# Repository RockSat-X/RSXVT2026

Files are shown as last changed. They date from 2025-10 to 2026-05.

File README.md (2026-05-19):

# Virginia Tech RockSat-X 2026 Project.

> [!IMPORTANT]
> Quick link to:
> - [Wallops Testing Procedure](#wallops-testing-procedure).
> - [Remove-Before-Flight Procedure](#remove-before-flight-procedure).
>
> Also check out the [RSXVT2026 Wiki](https://github.com/RockSat-X/RSXVT2026/wiki)!

&nbsp;

# Mission Overview.

Our experiment aims to evaluate the use of optical navigation
with Commercial-off-the-Shelf (COTS) products for use in spaceflight applications.
To conduct the experiment,
an autonomous attitude determination and control system (ADCS)
employing an optical navigation system (ONS)
will be designed to control a 1U CubeSat,
codenamed **Commercial Optical Navigation Satellite (CONSat)**.

The 2024 NASA Civil Space Shortfall Ranking lists 9 out of the top 30 shortfalls
as limitations with autonomous deep space navigation.
With recent advancements in computing and ML capabilities,
optical navigation could revolutionize deep space navigation.
Our team aims to address some of the challenges facing the space industry
by designing a cost-effective ADCS that would rely primarily on conditions
only available in deep space.

The CONSat vehicle's Optical Navigation System (ONS) has:
- OpenMV H7+.
- VN-100 IMU / AHRS.

The operating principle of the CONSat will be to:
1. Capture image and isolate target.
2. Perform LoS measurements to estimate attitude.
3. Blend LoS solution with IMU / AHRS solution.
4. Reorient spacecraft to align to target.

The target will be the Earth's horizon as seen at ~190 km apogee.

&nbsp;

# High-Level System Overview.

<p align="center">
<kbd>

<br>
<br>
<em>Deck-plate integrated experiment.</em>
<br>
<br>
</kbd>
</p>&nbsp;

<p align="center">
<kbd>
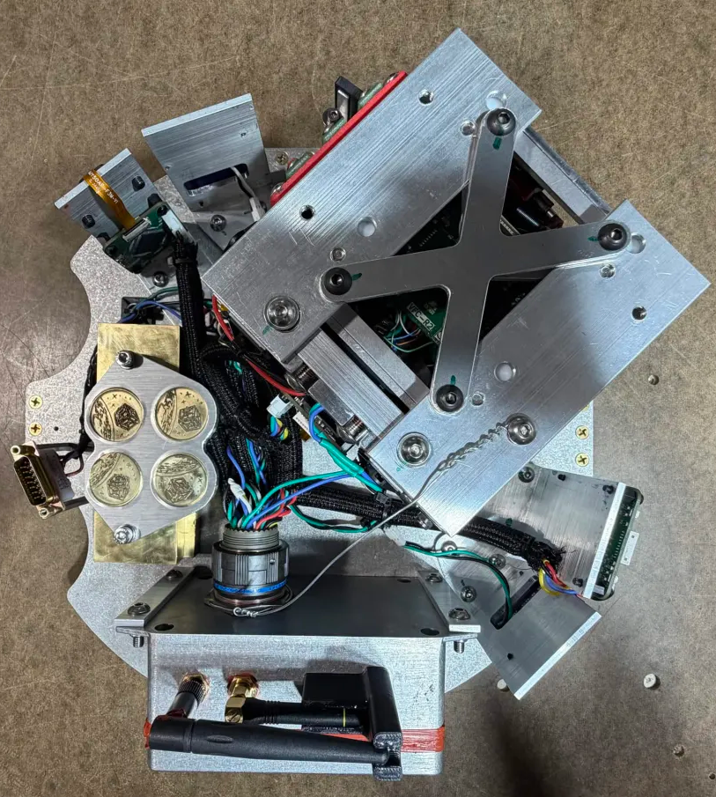
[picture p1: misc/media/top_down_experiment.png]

<br>
<br>
<em>Top-down view of the deck-plate integrated experiment.</em>
<br>
<br>
</kbd>
</p>&nbsp;

<p align="center">
<kbd>
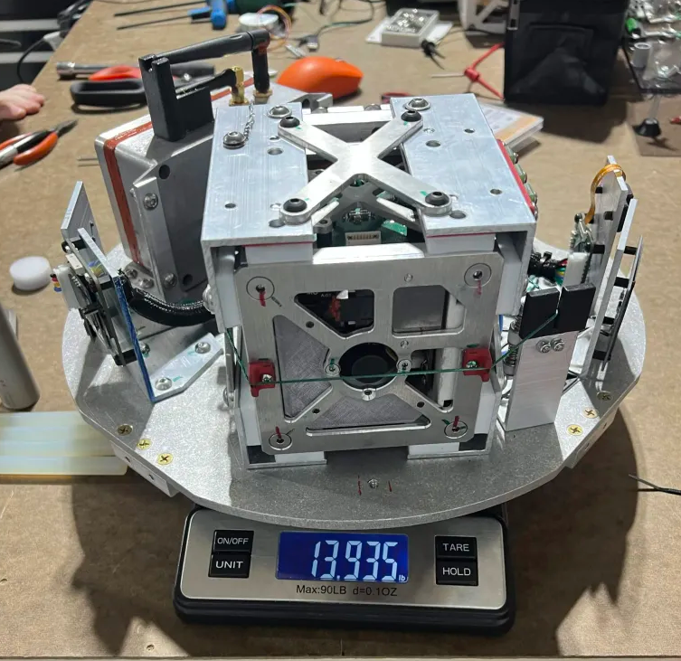
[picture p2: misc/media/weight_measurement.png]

<br>
<br>
<em>Weight of the deck-plate integrated experiment (13.935 pounds / 6.321 kilograms).</em>
<br>
<br>
</kbd>
</p>&nbsp;

<p align="center">
<kbd>
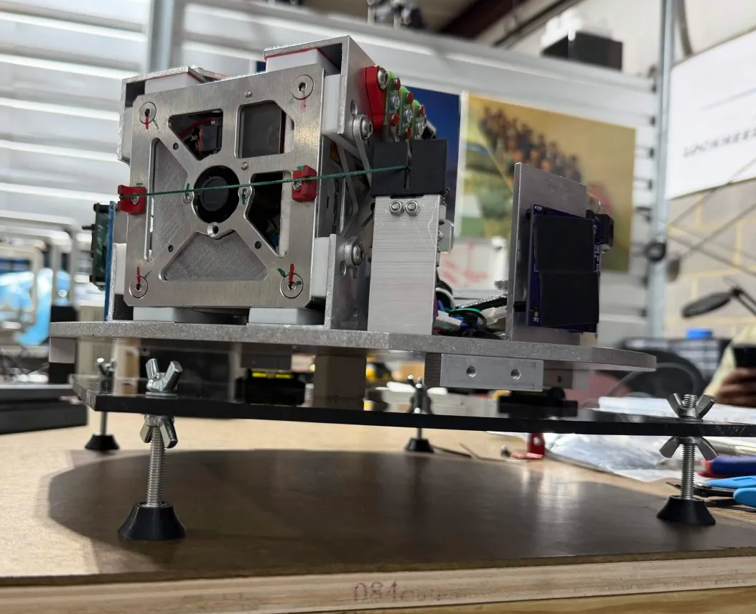
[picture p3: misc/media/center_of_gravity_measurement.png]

<br>
<br>
<em>Center of gravity of the deck-plate integrated experiment.</em>
<br>
<br>
</kbd>
</p>&nbsp;

<p align="center">
<kbd>
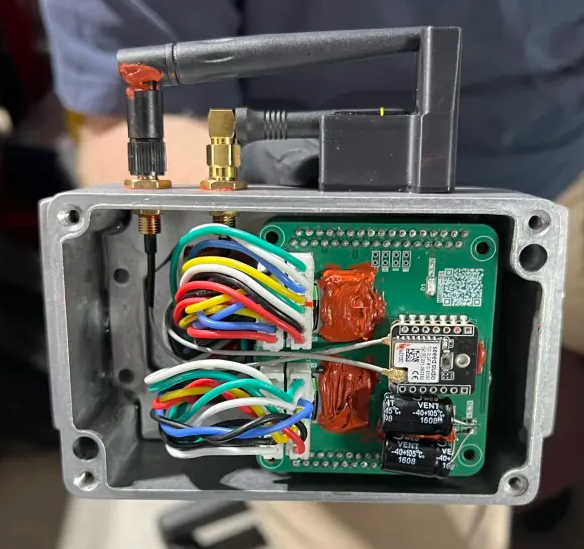
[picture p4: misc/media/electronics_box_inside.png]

<br>
<br>
<em>The inside of the main electronics box enclosure.</em>
<br>
<br>
</kbd>
</p>&nbsp;

<p align="center">
<kbd>
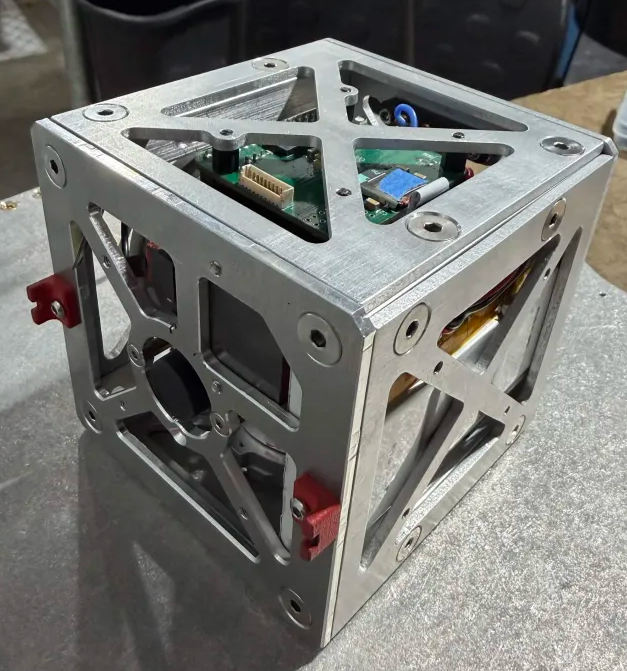
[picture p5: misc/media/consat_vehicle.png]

<br>
<br>
<em>CONSat vehicle.</em>
<br>
<br>
</kbd>
</p>&nbsp;

<p align="center">
<kbd>

<br>
<br>
<em>The inside of the CONSat vehicle.</em>
<br>
<br>
</kbd>
</p>&nbsp;

<p align="center">
<kbd>
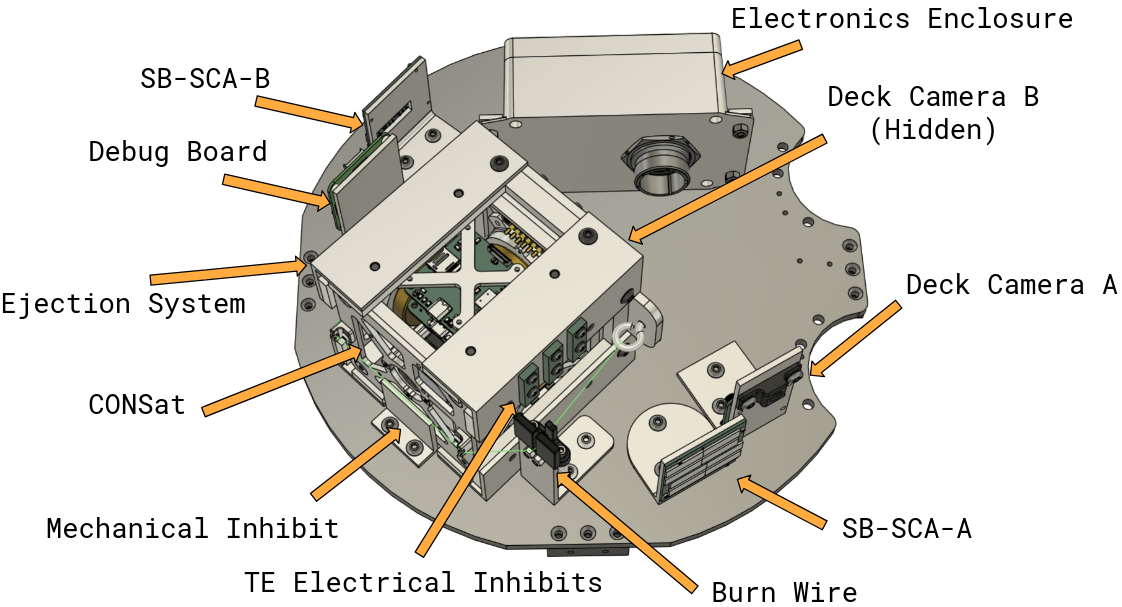
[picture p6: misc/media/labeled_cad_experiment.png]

<br>
<br>
<em>Labeled CAD model of the experiment.</em>
<br>
<br>
</kbd>
</p>&nbsp;

<p align="center">
<kbd>
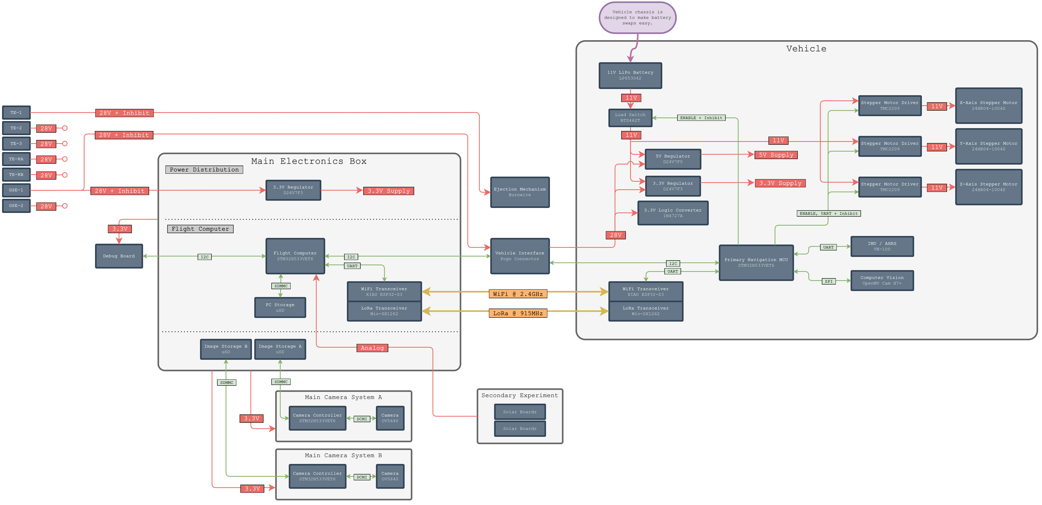
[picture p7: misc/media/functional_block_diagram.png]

<br>
<br>
<em>Functional block diagram of the CONSat experiment.</em>
<br>
<br>
</kbd>
</p>&nbsp;

## Main Camera System.

The experiment has two Main Camera Systems:
one placed before the ejection mechnism
and one next to a Solarboard by the burn-wire mechanism.

<p align="center">
<kbd>

<br>
<br>
<em>Main Camera System demonstration.</em>
<br>
<br>
</kbd>
</p>&nbsp;

The Main Camera System board has a single RGB LED.

| Color | Description |
| :---: | --- |
| White | Reformatting uSD card. |
| Magenta | Initializing uSD card. |
| Blue | Initializing OV5640 camera module. |
| Toggling green | Recording successfully. |
| Red | Main Camera System resetting. |

&nbsp;

The Main Camera System creates a binary blob file for each recording.
Use `cli.py parseVideo` to convert the binary blob file into an MP4 video.

&nbsp;

## Debug Board.

The Debug Board has a display to indicate the status of subsystems
from the perspective of the Main Flight Computer.
When the experiment is powered on via GSE-1,
the Debug Board will initialize and play the Nokia buzzer tune.
The display will also periodically invert color;
this is just to indicate that the Debug Board MCU is still running.

<p align="center">
<kbd>

<br>
<br>
<em>Debug board demonstration.</em>
<br>
<br>
</kbd>
</p>&nbsp;

The Debug Board displays the following information.

| Field | Description |
| :---: | --- |
| `DB-T` | Time elapsed since the debug board was powered on. |
| `MFC-T` | Time elapsed since the Main Flight Compiuter was powered on. |
| `SCB-A` | Voltage of SB-SCA. |
| `SCB-B` | Voltage of HP-SCA. |
| `te1` | Whether or not Main Flight Computer is detecting TE-1. |
| `vehicle` | Whether or not Main Flight Computer is communicating with the Vehicle Flight Computer through the vehicle interface. |
| `esp32` | Whether or not Main Flight Computer is receiving ESP-NOW data packets. |
| `lora` | Whether or not Main Flight Computer is receiving LoRa data packets. |
| `logger`  | Whether or not Main Flight Computer is saving data to its uSD card. |

If the Debug Board has not received the first debug packet from the Main Flight Computer yet,
then the field values will either be `???` or `nan` to indicate this.

> [!IMPORTANT]
> A known issue with the Debug Board's display is that it is not resettable.
> That is, if the Debug Board MCU has a communication issue with the display driver,
> there's a small possibility that the display ends up in a corrupted state.
> This may appear as the screen being darker, the resolution looking off,
> or is completely blank.
> The MCU has no way to fix this,
> but power-cycling will resolve this rare issue if it ever happens.

&nbsp;

The debug board has four RGB LEDs.

| Label | Position | Description |
| :---: | :---: | --- |
| `A` | Top Right | Flashes colors when the buzzer is being driven; this is just an extra indicator that's useful for when the buzzer is mute. |
| `B` | Top Left | White when the Main Flight Computer hasn't sent the first debug packet to the Debug Board yet; red when there's a bad status to be aware of such as the Main Flight Computer not having received RF data in a while. |
| `C` | Bottom Right | Toggles red when the Main Flight Computer hasn't sent a debug packet in a while; toggles green when a debug packet has been received. |
| `D` | Bottom Left  | White when the uSD card is being formatted; magenta when the Debug Board is failing to initialize the uSD card; toggles green periodically when data is successfully being logged to the uSD card. |

> [!IMPORTANT]
> If the Debug Board encounters an irrecoverable error,
> it'll panic and indicate this by flashing all LEDs red.
> The Debug Board should eventually reset itself and continue on as normal.

&nbsp;

The debug board plays the following buzzer tunes.

| Tune | Description |
| :---: | --- |
| [Nokia ](./misc/media/nokia.wav ) | Debug Board is initializing (e.g. just powered on from GSE-1). |
| [Hazard ](./misc/media/hazard.wav ) | Debug Board hasn't received a debug packet from the Main Flight Computer in a while. |
| [Up and Down](./misc/media/up_and_down.wav) | `te1` is active (i.e. burn-wire is going). |
| [Deep Beep  ](./misc/media/deep_beep.wav  ) | Main Flight Computer is reporting a bad status (e.g. haven't received RF data in a while) |
| [Tetris ](./misc/media/tetris.wave ) | The Debug Board's uSD card is being reformatted. |

To mute the buzzer, leave the header above the buzzer open.
To enable the buzzer, have a jumper shorting two adjacent pins;
which pins are shorted determines the volume of the buzzer.

&nbsp;

The uSD card is optional to the operation of the Debug Board.
The Debug Board uses LED D to indicate that it's successfully saving log data.

<p align="center">
<kbd>

<br>
<br>
<em>
To load a uSD card, lift the connector lid up,
<br>
place the uSD card,
and slide the lid down to secure it.
</em>
<br>
<br>
</kbd>
</p>&nbsp;

<p align="center">
<kbd>
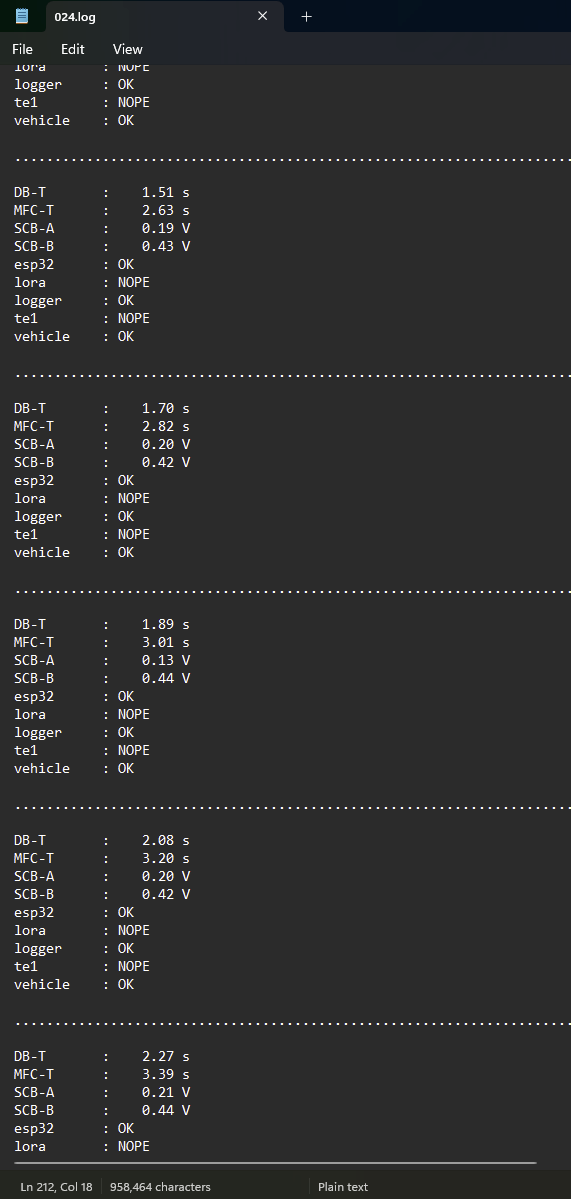
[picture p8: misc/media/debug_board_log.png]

<br>
<br>
<em>
The Debug Board creates an ASCII text file with <br>
the same information displayed on its screen.
</em>
<br>
<br>
</kbd>
</p>&nbsp;

## Vehicle Flight Computer.

The following table details the corresponding buzzer tune and RGB LED behavior for when a Vehicle Flight Computer diagnostic is reported.

| Severity | Tune | RGB LED | Description |
|:-:| :---: | :---: | --- |
| :bangbang: | [Ambulance  ](./misc/media/ambulance.wav ) | Fast toggling red | TMC2209 stepper motor drivers are failing initialization. This could be due to bad ribbon cable connection, dead batteries, inhibited batteries, or something else. |
| :warning: | [Heartbeat  ](./misc/media/heartbeat.wav ) | Slow toggling red | Vehicle Flight Computer has saturated a motor's RPM velocity. |
| :warning: | [Tetris ](./misc/media/tetris.wav ) | Slow toggling white | Vehicle Flight Computer is reformatting the uSD card. |
| :warning: | [Mario ](./misc/media/mario.wav ) | Fast toggling white | Resetting the Vehicle ESP32 due to an issue with it. |
| :warning: | [Three Tone ](./misc/media/three_tone.wav ) | Fast toggling white | Resetting the Vehicle OpenMV due to an issue with it. |
| :bangbang: | [Hazard ](./misc/media/hazard.wav ) | Fast toggling blue  | Communication issue with VN-100. |
| :white_check_mark: | [Nokia ](./misc/media/nokia.wav ) | Slow toggling white | Vehicle Flight Computer detecting that the vehicle has been redocked. |
| :white_check_mark: | [Birthday ](./misc/media/birthday.wav ) | Slow toggling white | Vehicle Flight Computer detecting that the vehicle has been ejected. |
| :warning: | [Heavy Beep ](./misc/media/heavy_beep.wav ) | Toggling magenta | Initialization issue with uSD card. This is okay if no uSD card is loaded. |
| :white_check_mark: | [Burp ](./misc/media/burp.wav ) | Blue blink | VN-100 communication okay. |
| :white_check_mark: | [Chirp ](./misc/media/chirp.wav ) | Green blink | uSD card logging okay. |
| :white_check_mark: | [Waking Up  ](./misc/media/waking_up.wav ) | None | Vehicle Flight Computer initializing (i.e. on activation of GSE-1); vehicle batteries are enabled at end of buzzer tune. |
| :white_check_mark: | [Star Wars  ](./misc/media/starwars.wav ) | None | Vehicle Flight Computer performing a dock shutdown (i.e. about to turn vehicle batteries off and resetting). |

| Severity | Description |
| :---: | --- |
| :bangbang:  | Something is likely very problematic and should be addressed as soon as possible. |
| :warning:  | A non-fatal or recoverable issue. |
| :white_check_mark:  | Positive or expected indicator of a working system. |

The three pin header on the Vehicle Flight Computer can be left open to mute the buzzer,
otherwise short a pair of adjacent pins to determine the volume of the buzzer.

&nbsp;

The Vehicle Flight Computer board also has an optional uSD card slot for log data.

<p align="center">
<kbd>
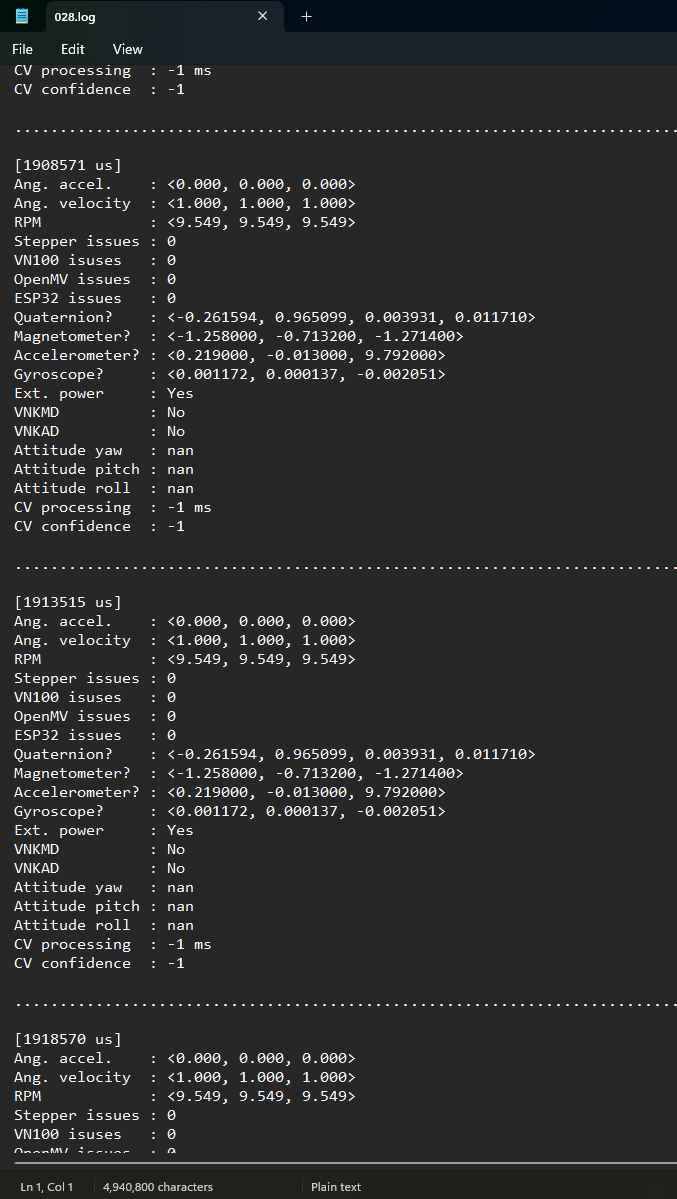
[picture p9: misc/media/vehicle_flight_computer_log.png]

<br>
<br>
<em>
The Vehicle Flight Computer creates an ASCII text file with information <br>
like VN-100 IMU data, CVT results, current motor velocities, and so on.
</em>
<br>
<br>
</kbd>
</p>&nbsp;

&nbsp;

## OpenMV H7+.

The OpenMV H7+ has a single RGB LED.

| RGB LED | Description |
| :---: | --- |
| Flashing blue | The CVT algorithm hasn't detected the horizon yet. |
| Flashing green | The CVT algorithm has found the horizon. |

Each toggle of the RGB LED represents an entire image being captured, processed, and transmitted to the Vehicle Flight Computer.
Because JPEG image compression is used,
if the OpenMV H7+'s camera lens is covered (e.g. by a finger),
the blinking of the RGB LED will be much faster.

If the OpenMV H7+'s RGB LED is not blinking, then it's very likely the program is not running,
but the Vehicle Flight Computer should reset the OpenMV H7+ eventually after a time-out period.

No other colors or behavior should be expected from the RGB LED or the OpenMV H7+ module as a whole.

&nbsp;

## Vehicle Power Distribution System.

The Vehicle Power Distribution System has LED indicators to be aware of.

| LED | Description |
| :---: | --- |
| Bright white | Vehicle interface providing power to the vehicle, thus this LED should be active if and only if the vehicle is docked and GSE-1 is active. |
| Yellow | Vehicle Flight Computer has enabled on-board battery power. The LED should be off when the Vehicle Flight Computer is initializing but should eventually turn on, unless the vehicle battery inhibit is in place, to which this LED will never turn on. |

The Vehicle Power Distribution System has three jumpers to be aware of.

<p align="center">
<kbd>
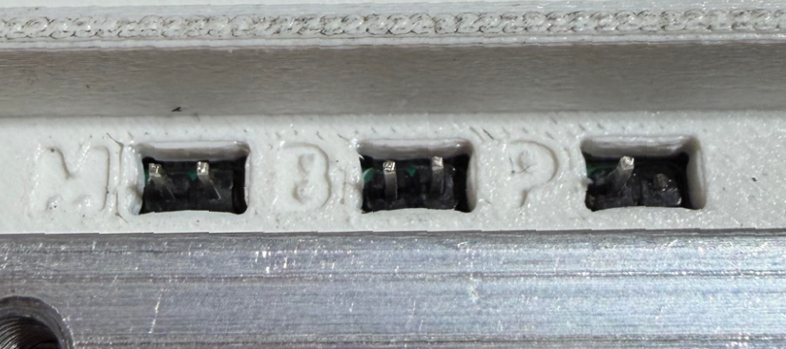
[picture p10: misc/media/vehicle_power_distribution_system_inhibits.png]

<br>
<br>
<em>
First jumper on the left denoted with "M" as in "Motor Inhibit". <br>
Second jumper in the middle denoted with "B" as in "Battery Inhibit". <br>
Third jumper on the right denoted with "P" as in "Power". <br>
Note that the third "Power" jumper should only have its <br>
first left pin and the second right pin is broken off.
</em>
<br>
<br>
</kbd>
</p>&nbsp;

| Jumper | Activation | Description |
| :---: | - | - |
| "M" | Use a shorting 2-pin jumper with pull tab. | Disable the control of the stepper motors. Vehicle Flight Computer can still initialize and operate, but reaction wheels will not spin. This is used to conserve battery charge, if needed. |
| "B" | Use a shorting 2-pin jumper with pull tab. | Disable the usage of the vehicle batteries. Vehicle Flight Computer can still initialize and operate via external power through the vehicle interface (i.e. GSE-1), but will immediately unpower upon being undocked. This can also be used to turn off the vehicle manually. |
| "P" | Use jumper wire to connect the pin to one of the vehicle batteries' positive terminal and wait several seconds. | Forces the usage of vehicle battery power, thus the Vehicle Flight Computer will initialize. This is to turn the vehicle on without relying on external power. |

> [!TIP]
> A quick way to turn off the vehicle is by using an Allen key to short the middle "B" jumper.

&nbsp;

# RF Verification.

During sequence testing and particularly GPS Roll-Out,
it's critical to verify that RF systems are working as intended
and to communicate this to NASA.

The easiest way to do this is to use the [Debug Board](#debug-board).
The screen will indicate if the Main Flight Computer is receiving RF data from the ESP32 and/or LoRa.
If the Debug Board is loaded with a uSD card,
the RF status will also be logged over time.

A more robust way to verify RF is to use the TinySA Spectrum Analyzer.
There are two particular frequency bands of interest.
| Link  | Center | Bandwidth | Start | End |
| :---: | :---: | :---: | :---: | :---: |
| ESP32 | 2.472 GHz | 20 MHz | 2.462 GHz | 2.482 GHz |
| LoRa  | 920 MHz | 125 kHz | 919.9375 MHz | 920.0625 MHz |

Configure the spectrum analyzer to observe these frequencies.

<p align="center">
</kbd>
<kbd>

<br>
<br>
<em>
Spectrum analyzer demonstration.
</em>
<br>
<br>
</kbd>
</p>&nbsp;

You should see a reading similar the following figures:

<p align="center">
<kbd>
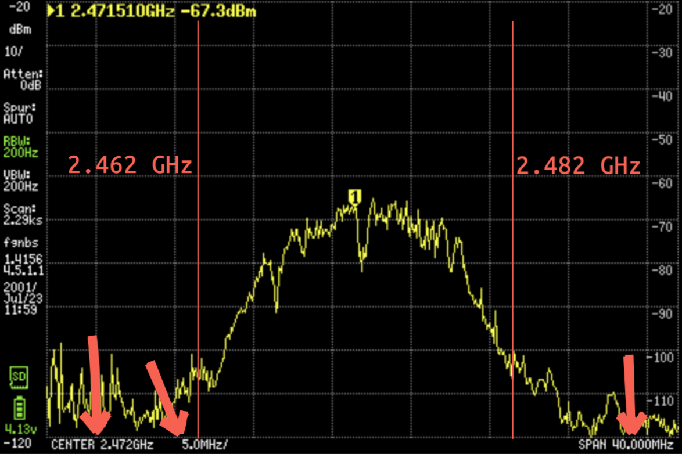
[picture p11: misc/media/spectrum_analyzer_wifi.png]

<br>
<br>
<em>
Spectrum analyzer measurement for the ESP32 link.
</em>
<br>
<br>
</p>
<p align="center">
</kbd>
<kbd>
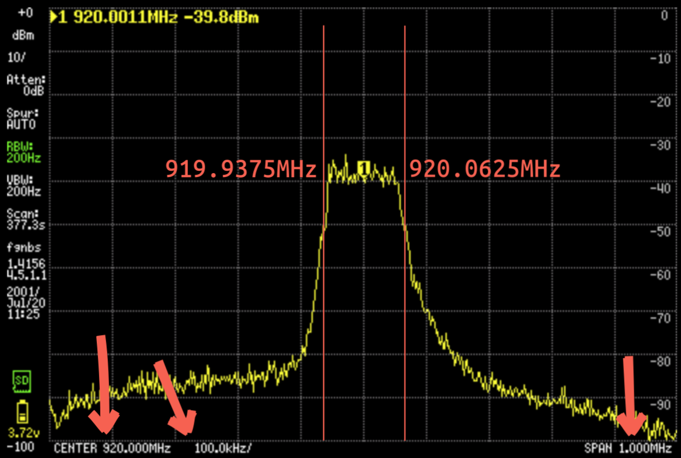
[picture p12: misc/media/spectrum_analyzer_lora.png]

<br>
<br>
<em>
Spectrum analyzer measurement for the LoRa link.
</em>
<br>
<br>
</kbd>
</p>&nbsp;

> [!IMPORTANT]
> The measurements shown in the figures were taken with an RBW value of 200 Hz;
> this makes the measurement more accurate but at the cost of being extremely slow.
> It's probably more productive to use an auto RBW value so measurements can be done quickly.
> Just as long there is an expected peak within frequency bands, all is good.

The RF verification process and expectations should be roughly as follows:

1. Before the experiment is powered on via GSE-1, no RF transmission is detected within the frequency bands.

2. Shortly after the experiment is powered on via GSE-1,
ESP32 and LoRa transmission can be seen within the frequency bands.

3. RF transmission is sustained for at least the duration of a full mission;
if applicable, the RF transmission should still be sustained even if the vehicle has ejected or becomes undocked.

4. RF transmission is sustained even when main has powered off (i.e. GSE-1 deactived)
as the vehicle will continue transmitting via battery power.

5. RF transmission is no longer detected once the vehicle has powered off
(either by using the vehicle battery inhibit or through a docked reset).

&nbsp;

# Wallops Testing Procedure.

The following table summarizes the primary configurations needed to be set for tests done at Wallops.

| Expected Date | Test | Allow Ejection? | Enable TE-1? | Enable Main GSE-1? | Enable Vehicle GSE-1? |
| :---: | :---: | :-: | :-: | :-: | :-: |
| May 17th, 2026; Sunday | Pre-Flight Seq. | :white_check_mark: | :white_check_mark: | :white_check_mark: | :white_check_mark: |
| May 18th-19th, 2026; Monday-Tuesday | Pre-Vibe All-Fire Seq. | :white_check_mark: | :white_check_mark: | :white_check_mark: | :white_check_mark: |
| May 18th-19th, 2026; Monday-Tuesday | Pre-Vibe No-Fire Seq. | :x: | :x: | :white_check_mark: | :white_check_mark: |
| May 19th, 2026; Tuesday | Pre-Vibe Back Up Seq. | :x: | :x: | :white_check_mark: | :white_check_mark: |
| May 20th-21st, 2026; Wednesday-Thursday | Vibration Testing | :white_check_mark: | :white_check_mark: | :white_check_mark: | :white_check_mark: |
| May 22nd, 2026; Friday | Post-Vibe All-Fire Seq. | :white_check_mark: | :white_check_mark: | :white_check_mark: | :white_check_mark: |
| May 22nd, 2026; Friday | Post-Vibe No-Fire Seq. | :x: | :x: | :white_check_mark: | :white_check_mark: |
| May 22nd, 2026; Friday | Post-Vibe Back Up Seq. | :x: | :x: | :white_check_mark: | :white_check_mark: |
| May 22nd, 2026; Friday | GPS Roll-Out | :x: | :x: | :white_check_mark: | :white_check_mark: |
| June 19th, 2026; Friday | Final All-Fire Seq. | :white_check_mark: | :white_check_mark: | :white_check_mark: | :white_check_mark: |
| June 19th, 2026; Friday | Final No-Fire Seq. | :x: | :x: | :white_check_mark: | :white_check_mark: |
| June 19th, 2026; Friday | Final Back Up Seq. | :x: | :x: | :white_check_mark: | :white_check_mark: |

To allow ejection ( :white_check_mark: ),
ensure the mechanical inhibit in front of the ejection mechanism is removed.

To prevent ejection ( :x: ),
ensure the mechanical inhibit is secured in front of the ejection mechanism.

To have TE-1, Main GSE-1, or Vehicle GSE-1 be enabled ( :white_check_mark: ),
insert a screw into the corresponding electrical screw switch on the side of the ejection mechanism.
Verify short-circuit with a multimeter.

To have TE-1, Main GSE-1, or Vehicle GSE-1 be disabled ( :x: ),
ensure a screw is not inserted into the corresponding electrical screw switch.
Verify open-circuit with a multimeter.

> [!IMPORTANT]
> The experiment must be put into flight-ready configuration during vibration testing.
> This means all electrical screw switches should be enabled and no mechanical inhibit present.
> Any loose components such as external uSD cards and jumpers should be removed (see [RBF procedures](#remove-before-flight-procedure)).
> Screws should be applied with blue Loctite.
>
> It should also be noted that Wallops will only provide GSE-1 and there will be no TE-1 power
> during this vibration test (this also applies to GPS Roll-Out).

> [!IMPORTANT]
> The purpose of the electrical screw switches for Main GSE-1 and Vehicle GSE-1 is for flexibility.
> In the event that we need to ensure that the main avionics and/or vehicle does not power on,
> we have these as a way to do so.

&nbsp;

# Remove-Before-Flight Procedure.

The following steps are to be carried out in order with minimal deviations after all final sequence tests are done.

> [!IMPORTANT]
> Pre-RBF procedure checklist:
> - Multimeter.
> - Three fully charged EEMB LP653042 3.7V 820mAh batteries.
> - Allen key kit.
> - Red Loctite.
> - Tweezers.
> - Needle-nose pliers.
> - Phillips screwdriver.

&nbsp;

## 1. Take out vehicle.

Remove the ejection inhibit if still in place.
The ejection inhibit will not be used again,
so store it away in a secure location.

Take out the burn-wire mechanism in order to release the vehicle from the ejection mechanism.
Place the burn-wire mechanism in a secure location.

Carefully undock vehicle and place it down on a table to be worked on.

&nbsp;

## 2. Replace vehicle batteries.

Go to the side of the vehicle where the batteries are stored.

<p align="center">
<kbd>
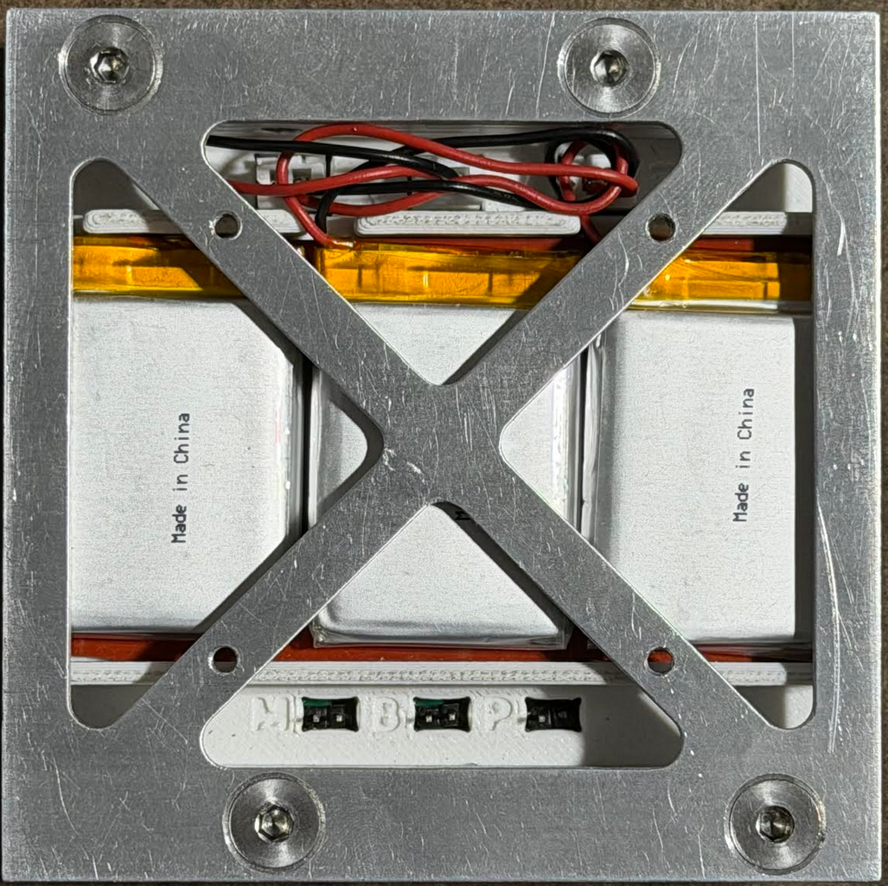
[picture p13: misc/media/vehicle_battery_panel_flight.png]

<br>
<br>
<em>
Side of the vehicle where the batteries are stored.
</em>
<br>
<br>
</kbd>
</p>&nbsp;

Take off the panel.
Place the panel and screws in a secure location.

<p align="center">
<kbd>
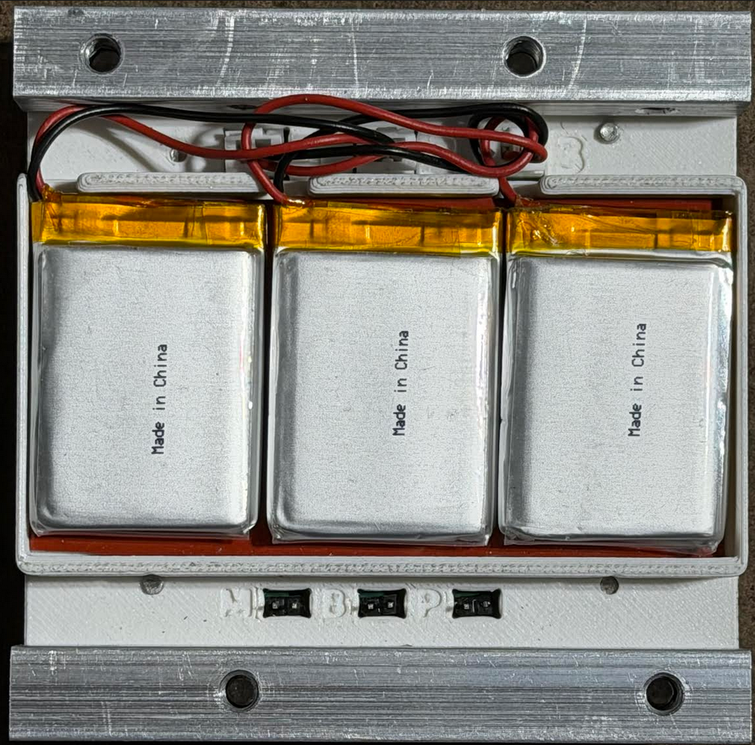
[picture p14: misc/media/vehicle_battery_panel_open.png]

<br>
<br>
<em>
Panel that secured the vehicle's batteries removed.
</em>
<br>
<br>
</kbd>
</p>&nbsp;

Take out the old vehicle batteries.
It is okay to tug on the cable to do so if excessive force is not used.
Make sure to place the old vehicle batteries somewhere secure so it will not be confused with the new batteries.

<p align="center">
<kbd>
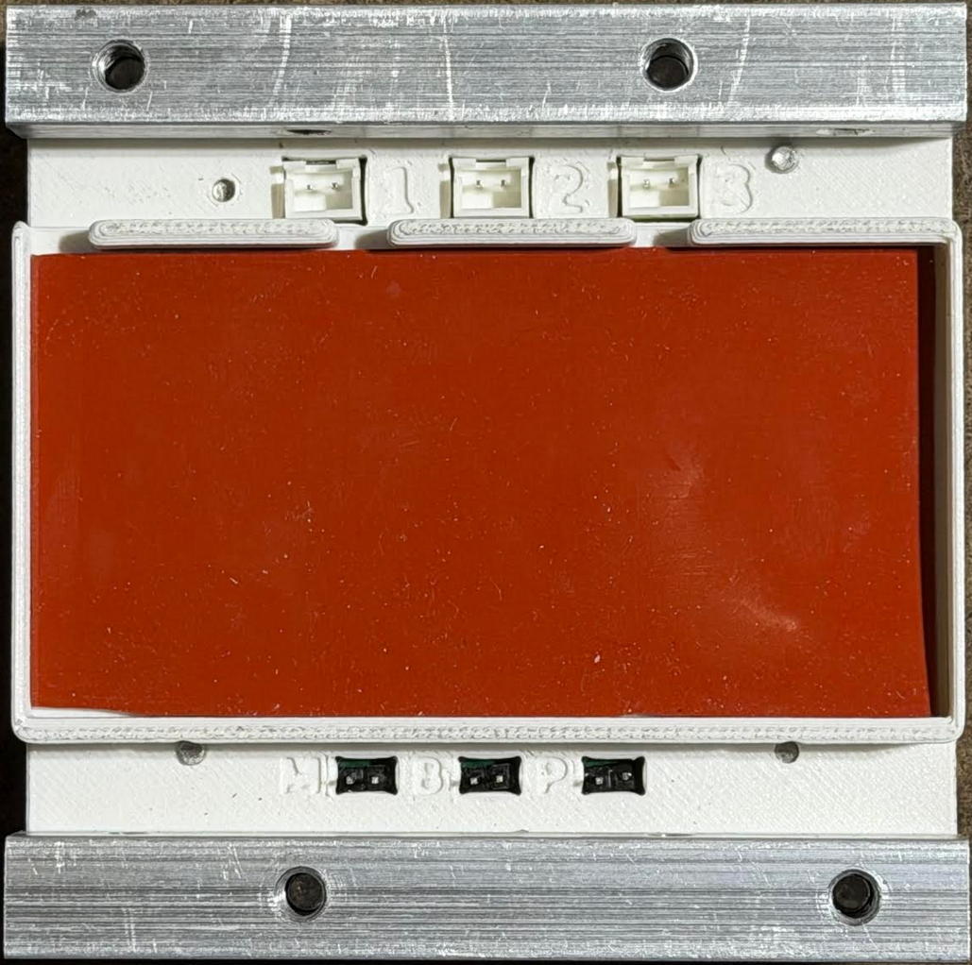
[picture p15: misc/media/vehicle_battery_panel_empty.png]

<br>
<br>
<em>
Vehicle batteries removed.
</em>
<br>
<br>
</kbd>
</p>&nbsp;

Verify that the new batteries (EEMB LP653042 3.7V 820mAh) are fully charged.

<p align="center">
<kbd>
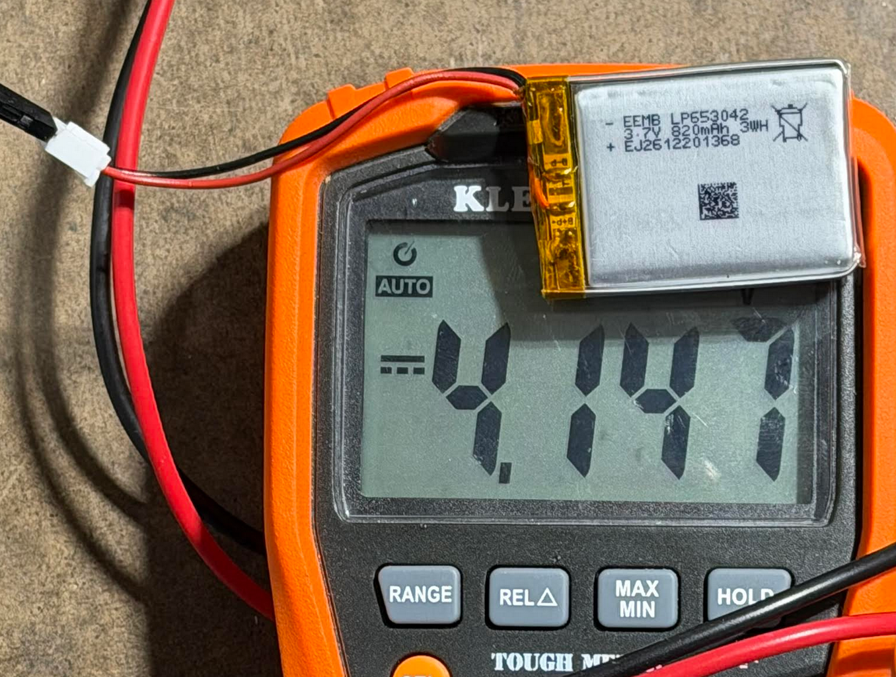
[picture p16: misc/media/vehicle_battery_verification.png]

<br>
<br>
<em>
A fully charged vehicle battery should have at least 4V.
</em>
<br>
<br>
</kbd>
</p>&nbsp;

Verify that the new batteries have a JST-XH plug of the correct polarity.

<p align="center">
<kbd>
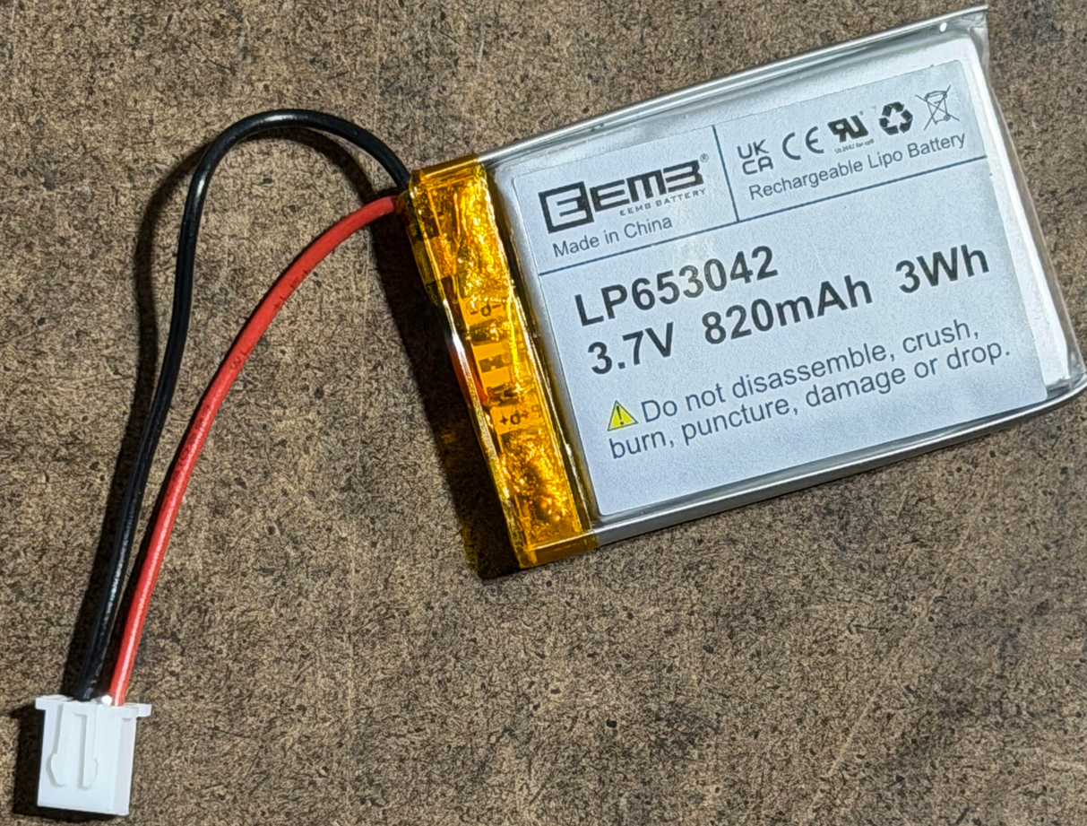
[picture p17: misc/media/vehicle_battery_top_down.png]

<br>
<br>
<em>
Note the plug polarity.
</em>
<br>
<br>
</kbd>
</p>&nbsp;

Put in the new vehicle batteries.
The order in which the vehicle batteries are connected does not matter.
Ensure the cables are well tucked to prevent them being crushed by the panel.

<p align="center">
<kbd>

<br>
<br>
<em>
Vehicle batteries replaced.
</em>
<br>
<br>
</kbd>
</p>&nbsp;

Place and align the vehicle panel with the pillar's screw holes and verify
that the battery cables will not be crushed.

<p align="center">
<kbd>
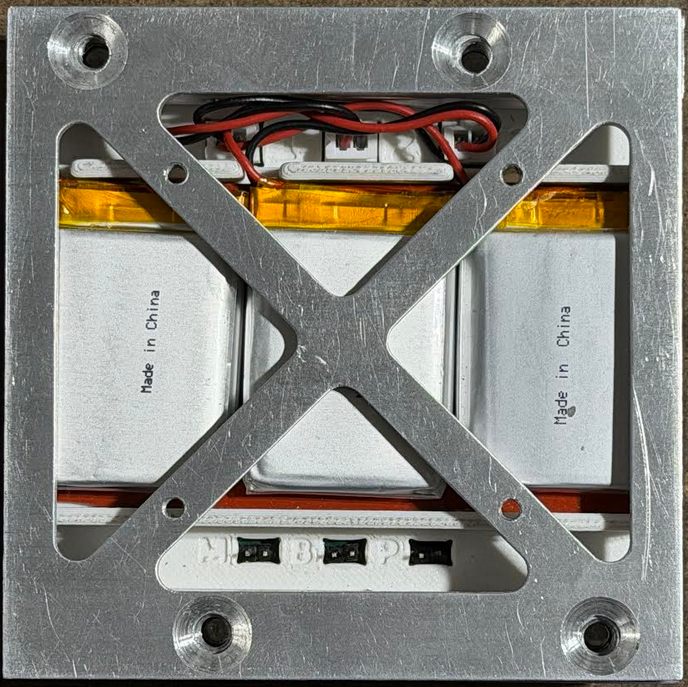
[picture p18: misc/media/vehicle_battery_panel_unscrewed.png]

<br>
<br>
<em>
Vehicle panel aligned on top but not yet screwed.
</em>
<br>
<br>
</kbd>
</p>
<p align="center">
<kbd>
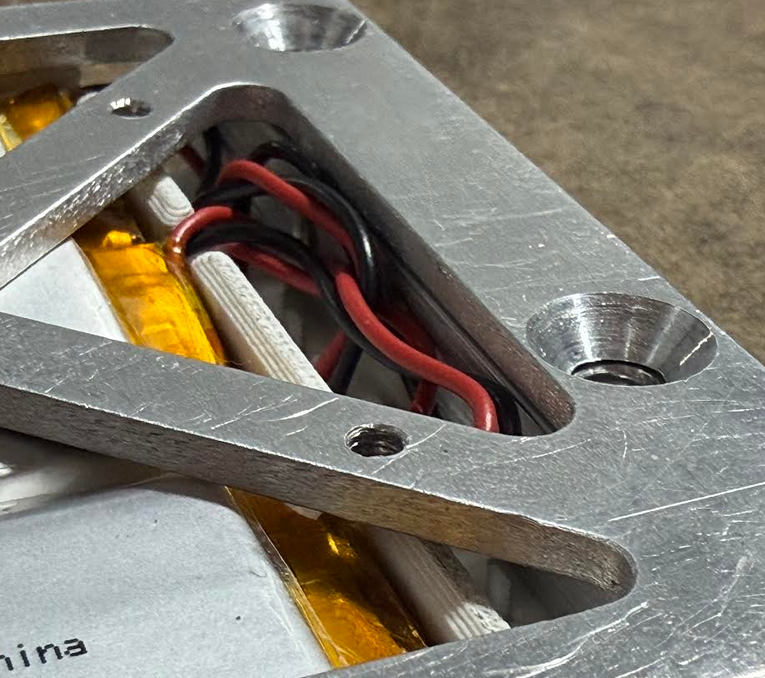
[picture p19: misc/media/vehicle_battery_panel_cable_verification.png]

<br>
<br>
<em>
Battery cables tucked securely and not between the panel and pillar.
</em>
<br>
<br>
</kbd>
</p>&nbsp;

Apply red Loctite to the threads and reinsert screws to secure the panel.

<p align="center">
<kbd>

<br>
<br>
<em>
Side of the vehicle where the batteries are stored.
</em>
<br>
<br>
</kbd>
</p>&nbsp;

## 3. Remove vehicle jumper inhibits.

Ensure the vehicle's jumpers for disabling motors, disabling batteries, and forcing vehicle power-on
are all open-circuit as depicted below.

<p align="center">
<kbd>

<br>
<br>
<em>
Vehicle jumpers in flight configuration.
</em>
<br>
<br>
</kbd>
</p>&nbsp;

## 4. Redock vehicle.

Reinsert vehicle into the ejection mechanism.
Make certain that the vehicle is in the correct orientation.
Verify that the vehicle interface connectors are aligned.

Put the previously removed burn-wire mechanism
back onto the deck-plate to secure the vehicle in the ejection mechanism.
Apply red Loctite to screws during this process.

Visually verify and test that the vehicle is well secured
by the ejection mechanism and burn-wire rope.

&nbsp;

## 5. Remove external uSD connector lids and jumpers.

To prevent vibration risks,
the Vehicle Flight Computer and Debug Board should have the lid of their uSD connectors be taken off.
The pin header for the buzzer should also be left as an open circuit.

<p align="center">
<kbd>
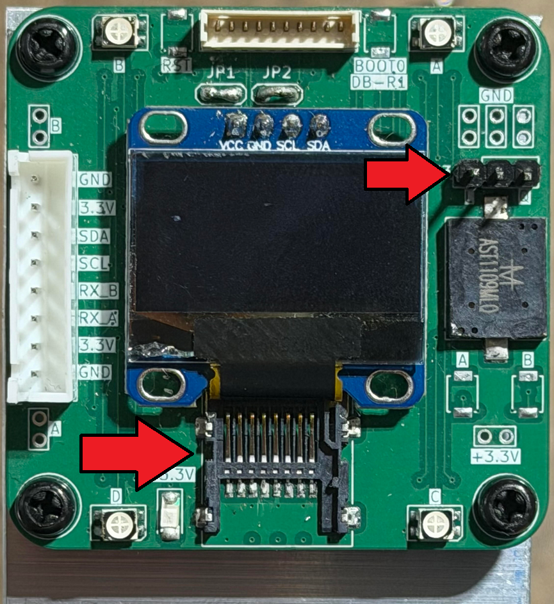
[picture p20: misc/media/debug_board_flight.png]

<br>
<br>
<em>
Debug Board without uSD card connector lid and buzzer jumper.
</em>
<br>
<br>
</kbd>
</p>&nbsp;

<p align="center">
<kbd>
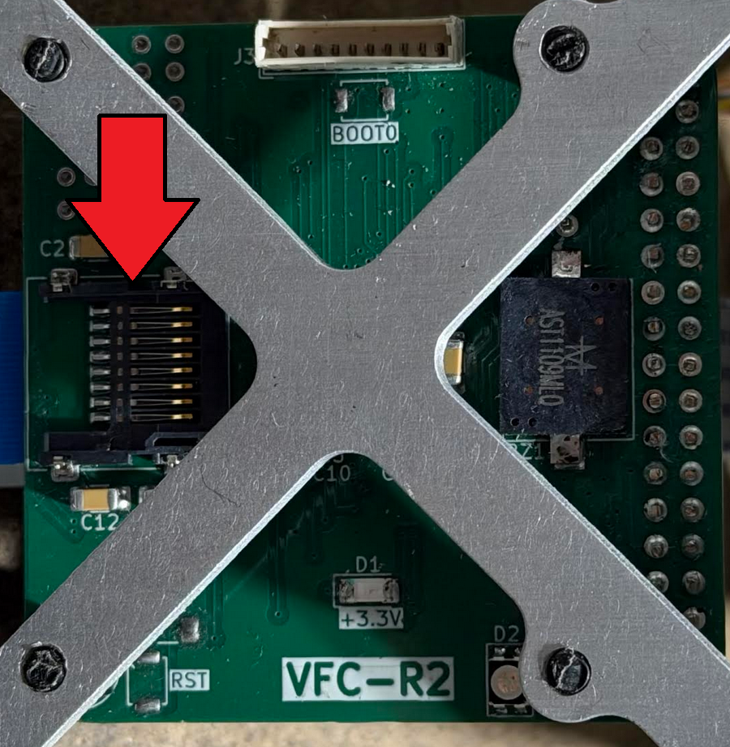
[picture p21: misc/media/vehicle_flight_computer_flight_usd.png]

<br>
<br>
<em>
Vehicle Flight Computer without uSD card connector lid.
</em>
<br>
<br>
</kbd>
</p>&nbsp;

<p align="center">
<kbd>
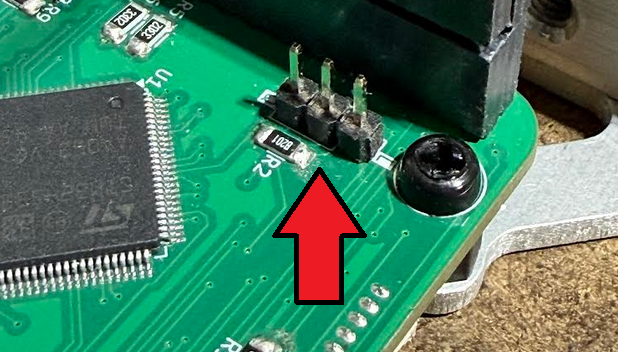
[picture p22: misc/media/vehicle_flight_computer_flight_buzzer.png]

<br>
<br>
<em>
Vehicle Flight Computer without buzzer jumper. <br>
Tweezers might be needed.
</em>
<br>
<br>
</kbd>
</p>&nbsp;

## 6. Enable electrical screw switches.

Insert screws with red Loctite into the three electrical screw switches
on the side of the ejection mechanism.

Verify connectivity of each electrical screw switch
by testing continuity of the two pads.

&nbsp;

## 7. Final checks.

> [!IMPORTANT]
> Verify that the following has been done:
> - New vehicle batteries has been put in.
> - Red Loctite has been applied to the vehicle's panel on the battery side.
> - Red Loctite has been applied to the burn-wire mechanism.
> - Red Loctite has been applied to the electrical screw switches.
> - Vehicle is well secured by the burn-wire rope and ejection mechanism as a whole.
> - No loose components like uSD card connector lids or jumpers are in place.
> - Electrical screw switches have the expected connectivity.

&nbsp;

# Burn-Wire Line Assembly.

These instructions describe how to fabricate the burnwire restraint lines
using 1 mm braided line and two overhand loop knots.

The finished burnwire line should have:
- Two looped ends.
- Approximately 12.75 in finished length.
- ±0.5 inch allowable tolerance.

Required materials:
- Tape measure.
- Dorisea Extreme Braid, 300 lb, 1 mm.
- Good scissors or sharp knife.

Use an _**Overhand Loop Knot**_ for both ends ([video tutorial](https://www.youtube.com/watch?v=7LSOyXJeUog)).

<p align="center">
<kbd>
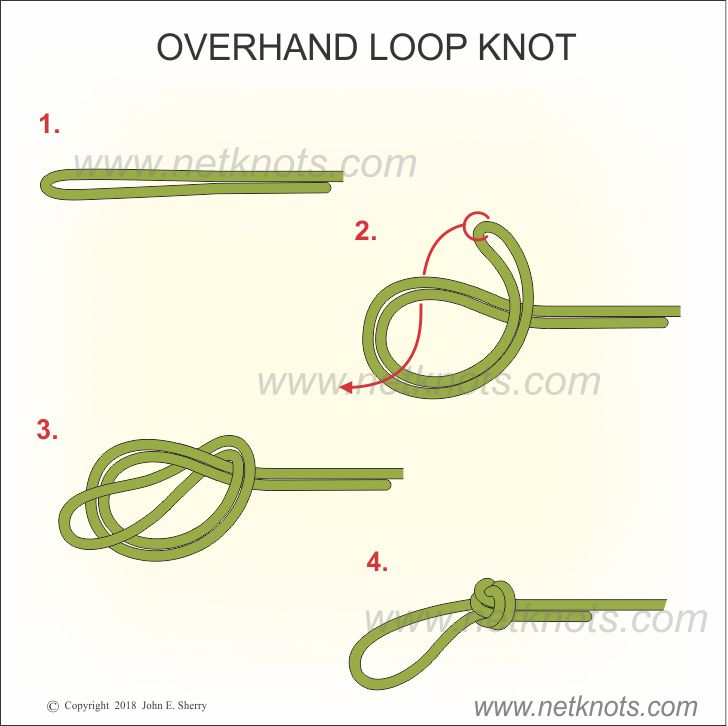
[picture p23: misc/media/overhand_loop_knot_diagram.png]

<br>
<br>
<em>
Overhand loop knot reference diagram.
</em>
<br>
<br>
</kbd>
</p>&nbsp;

## 1. Tie first loop.

Tie an overhand loop knot at the end of the line.
Target loop length of approximately 1 inch.
Leave a short tail after tightening the knot.

<p align="center">
<kbd>
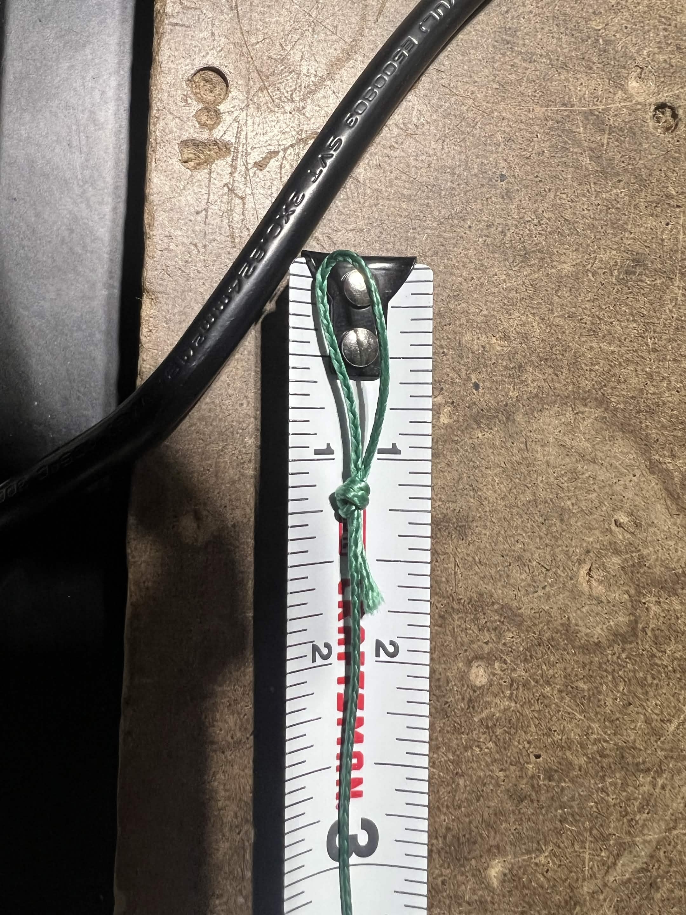
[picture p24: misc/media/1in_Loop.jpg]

<br>
<br>
<em>
1 inch loop.
</em>
<br>
<br>
</kbd>
</p>&nbsp;

## 2. Measure length.

Using the tape measure, measure _**13.5 inches from the tip of the loop**_.
Mark this location with a marker.

> [!IMPORTANT]
> _**Do NOT cut the line yet.**_

<p align="center">
<kbd>
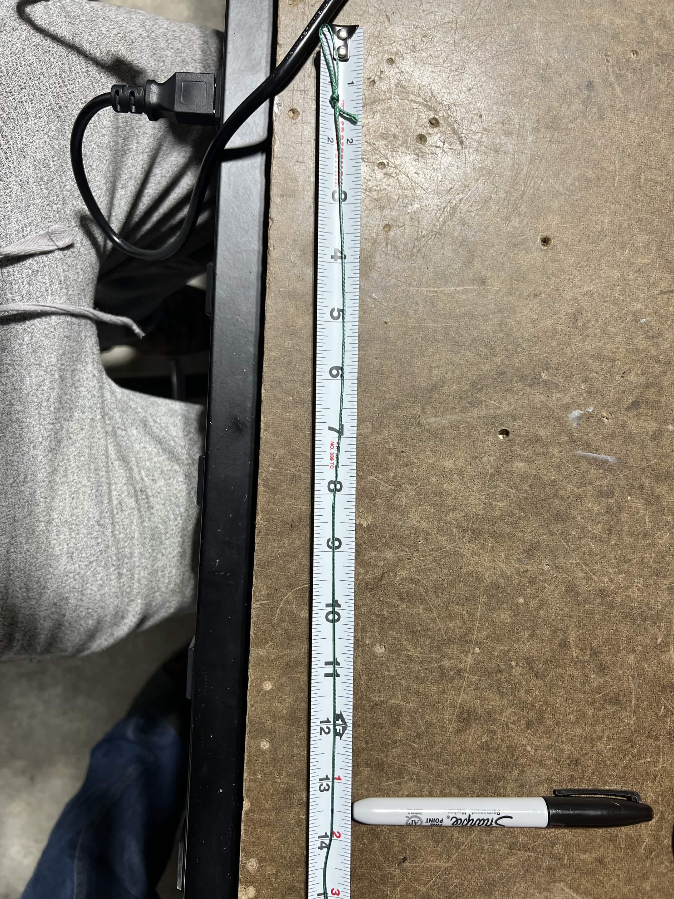
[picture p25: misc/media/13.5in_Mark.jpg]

<br>
<br>
<em>
13.5 inch mark.
</em>
<br>
<br>
</kbd>
</p>&nbsp;

## 3. Fold the line.

Fold the line in half at the 13.5 inch mark.
Ensure the marked location becomes the tip of the second loop.

<p align="center">
<kbd>
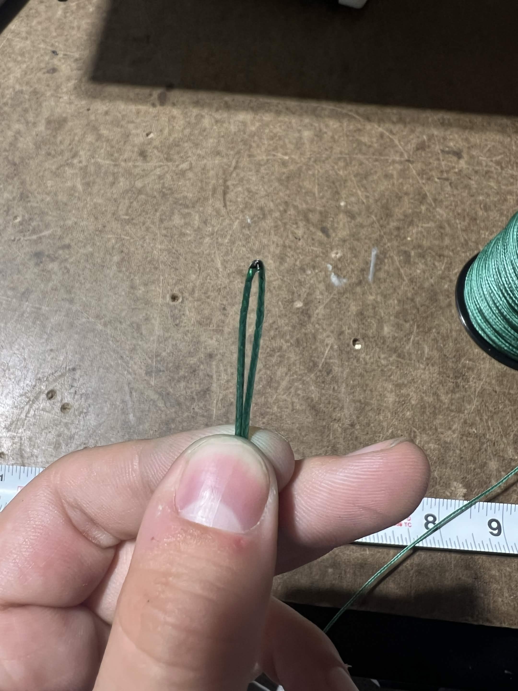
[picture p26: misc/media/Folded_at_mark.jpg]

<br>
<br>
<em>
Folded at mark.
</em>
<br>
<br>
</kbd>
</p>&nbsp;

## 4. Tie second loop.

Tie another overhand loop knot.
Loop length should again be approximately 1 inch.
Ensure the black mark is positioned at the tip of the loop before tightening.

<p align="center">
<kbd>
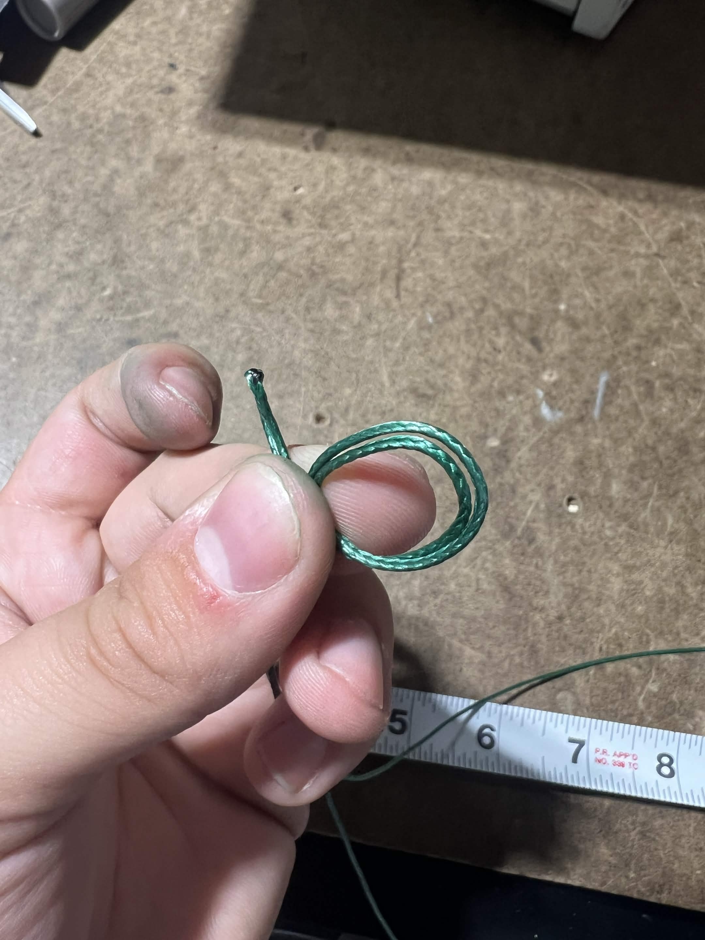
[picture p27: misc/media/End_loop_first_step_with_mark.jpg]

<br>
<br>
<em>
End loop first step.
</em>
<br>
<br>
</kbd>
</p>&nbsp;

<p align="center">
<kbd>
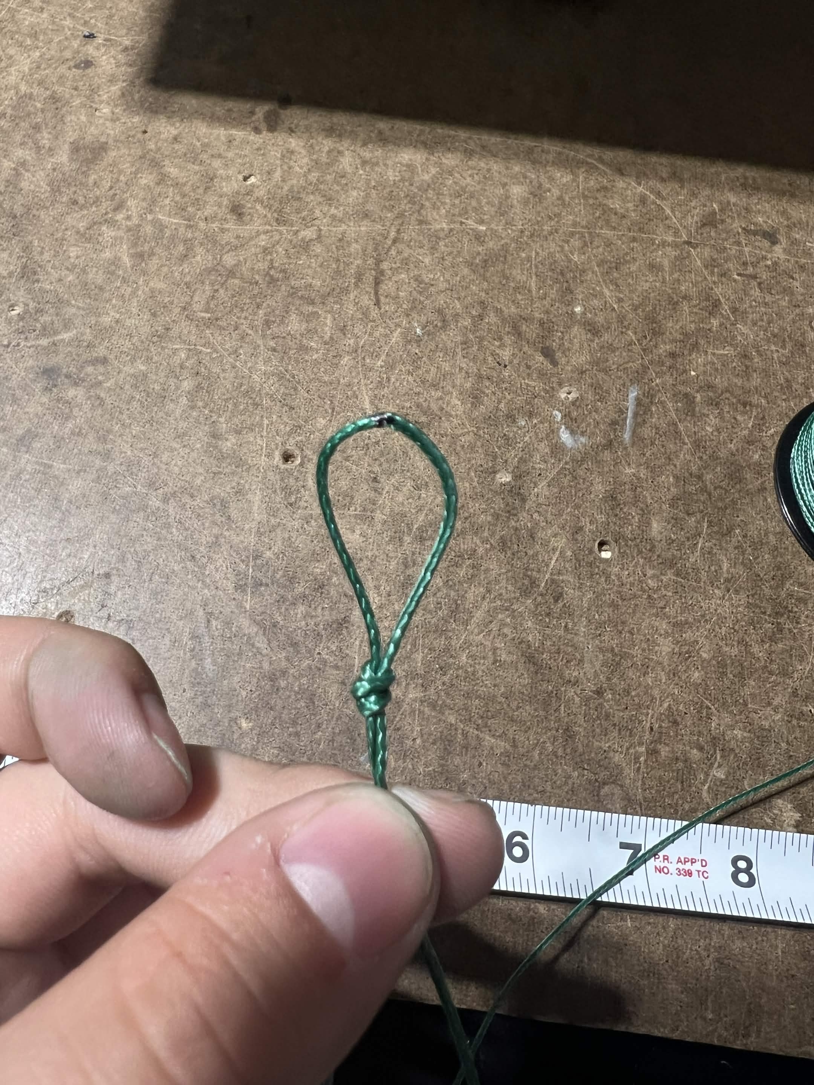
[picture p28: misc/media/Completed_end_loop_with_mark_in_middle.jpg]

<br>
<br>
<em>
Completed end loop.
</em>
<br>
<br>
</kbd>
</p>&nbsp;

## 5. Cut from roll.

Cut the line free from the spool.
Leave approximately 0.25 inch tail on the final knot.

<p align="center">
<kbd>
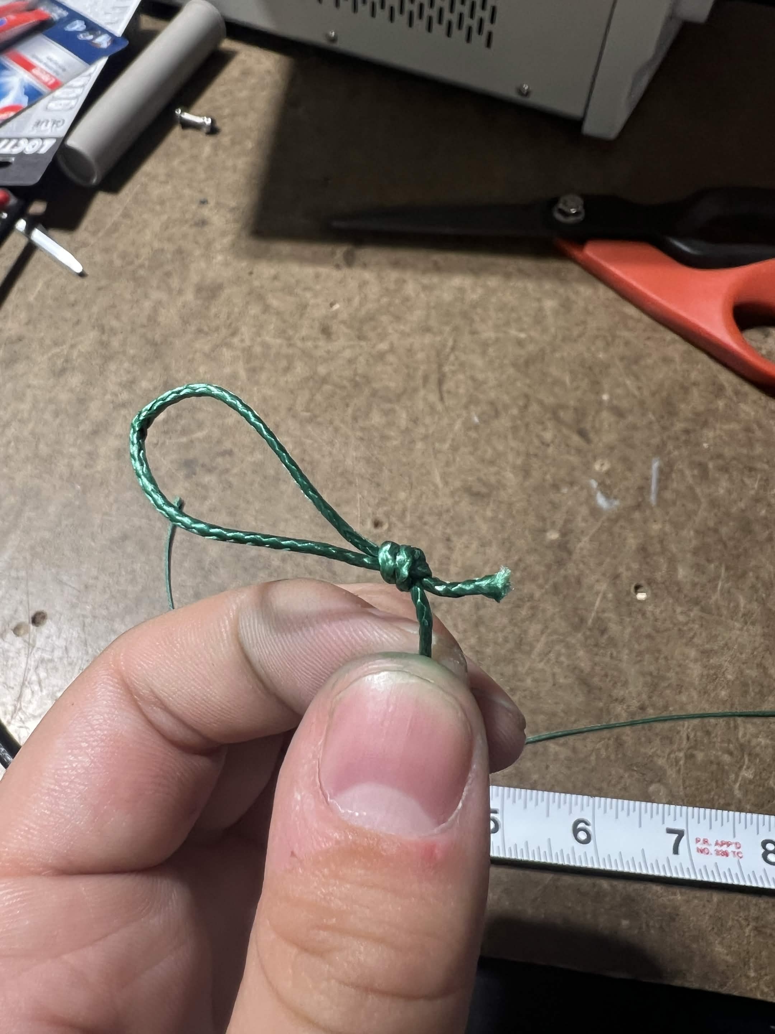
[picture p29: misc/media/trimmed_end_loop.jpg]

<br>
<br>
<em>
Trimmed end loop.
</em>
<br>
<br>
</kbd>
</p>&nbsp;

## 6. Final inspection.

Verify the completed burnwire line length.
Finished length of 12.75 ± 0.5 inches.
Measure from loop tip to loop tip.

<p align="center">
<kbd>
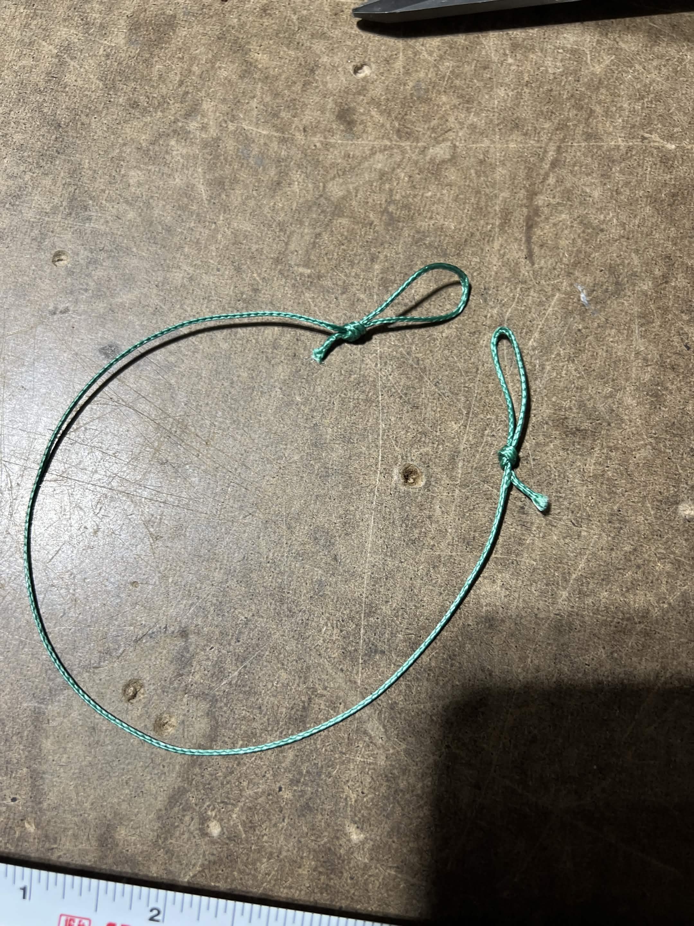
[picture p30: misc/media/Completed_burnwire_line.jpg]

<br>
<br>
<em>
Completed burn-wire line.
</em>
<br>
<br>
</kbd>
</p>&nbsp;

<p align="center">
<kbd>
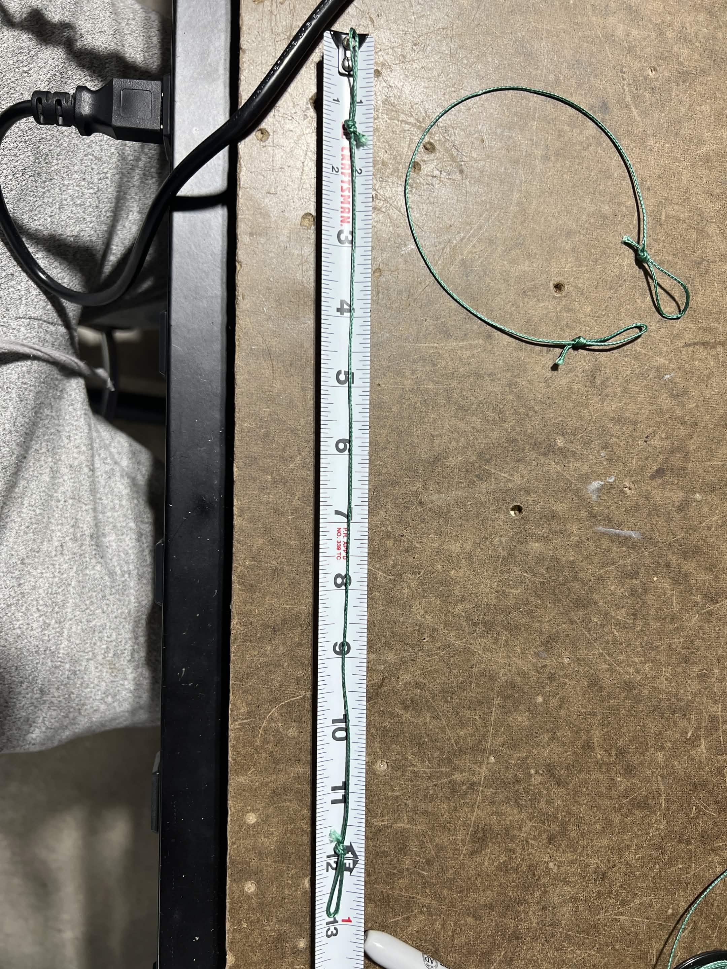
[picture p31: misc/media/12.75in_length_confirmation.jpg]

<br>
<br>
<em>
12.75in length confirmation.
</em>
<br>
<br>
</kbd>
</p>&nbsp;

A completed burnwire line is acceptable if:

- Both loops are securely tied using overhand loop knots.
- Both loops are approximately 1 inch long.
- Knot tails are trimmed to approximately 0.25 inch.
- Final overall length is 12.75 ± 0.5 in.
- Knots are fully tightened and seated cleanly.

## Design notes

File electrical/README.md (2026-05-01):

# Production-Ready Status.

The following list below are files considered "production-ready".
This is an informal status given to the code to essentially say
that bugs and errors from them are unlikely and should not be expected.
New features, API changes, etc. can also be expected to be much less frequent,
and if any changes are made,
careful documentation and testing will be done to validate them.

> #### `ringbuffer.c`
> 
> The ring-buffer implementation is **production-ready**.
> Issues concerning usage and behavior of ring-buffers are unlikely.
>
> \- *Phuc Doan. February 22nd, 2026.*

> #### `timekeeping.c`
>
> The driver for keeping track of elapsed time with microsecond granularity is **production-ready**.
> Timer accuracy is not accounted for in this implementation,
> but for our application, this should be fine.
>
> \- *Phuc Doan. February 25th, 2026.*

> #### `sd_initer.c`
>
> The state-machine implementation for initializing SD cards is **production-ready**.
> The implementation is not guaranteed to support all SD cards,
> but all error conditions are well-defined and handled accordingly.
> Issues concerning usage and behavior of the SD-initer are unlikely.
>
> \- *Phuc Doan. February 22nd, 2026.*

> #### `sd_cmder.c`
>
> The state-machine implementation for handling SDMMC transfers is **production-ready**.
> The implementation is harden towards hardware issues,
> such as unexpected SD card ejection/reinsertion.
> Hardware issues such as card glitches are still possible,
> but the state-machine is designed to be easily resettable in such rare events.
> Issues concerning usage and behavior of the SD-cmder are unlikely.
>
> \- *Phuc Doan. February 23rd, 2026.*

> #### `sd.c`
>
> The API for doing read/writes to SD cards is **production-ready**.
> Issues concerning usage and behavior of the SD API are unlikely.
>
> \- *Phuc Doan. February 23rd, 2026.*

> #### `ovcam.c`
>
> The driver for the OV5640 camera module is **production-ready**.
> The register initialization sequence is open to being modified.
> The driver is designed to work with the OV5640 module specifically,
> but other compatiable camera modules may work too.
> Issues concerning usage and behavior of the OVCAM driver are unlikely.
>
> \- *Phuc Doan. February 25th, 2026.*

> #### `uxart.c`
>
> The driver for UART communication is **production-ready**.
> Because of how simple the interface is,
> the implementation does not raise any error conditions to the user;
> checksums in any data-transfer should be sufficient.
> Operationally, the driver should behave as expected
> when doing full-duplex and half-duplex transfers.
>
> \- *Phuc Doan. February 26th, 2026.*

> #### `buzzer.c`
>
> The buzzer driver is **production-ready**.
> It's pretty simple.
> There shouldn't be any issues with it.
> Hopefully.
>
> \- *Phuc Doan. February 26th, 2026.*

> #### `ssd1306.c`
>
> The driver for displays controlled by SSD1306 is **production-ready**.
> Main known issue is that there's no fool-proof
> way to reset the SSD1306 without power-cycling.
> Nonetheless, a misconfigured SSD1306 will only happen under extreme I2C bus mishaps,
> and should not be catastrophic to the user.
>
> \- *Phuc Doan. March 1st, 2026.*

> #### `stepper.c`
>
> The driver for controlling TMC2209 stepper motor drivers is **production-ready**.
> Register settings for the TMC2209s should not be changed to avoid accidentally frying components.
>
> \- *Phuc Doan. April 28th, 2026.*

> #### `spi.c`
>
> The driver for SPI data reception is **production-ready**.
> The implementation is very narrow in scope,
> but should be sufficient for our project.
> Issues concerning usage and behavior of the SPI driver are unlikely.
>
> \- *Phuc Doan. April 28th, 2026.*

> #### `i2c.c`
>
> The driver for I2C communication is **production-ready**.
> Issues concerning usage and behavior of the I2C driver are unlikely.
>
> \- *Phuc Doan. April 28th, 2026.*

Files not listed above are not considered **production-ready**.
This does not mean they are unusable, just that development is still undergoing.

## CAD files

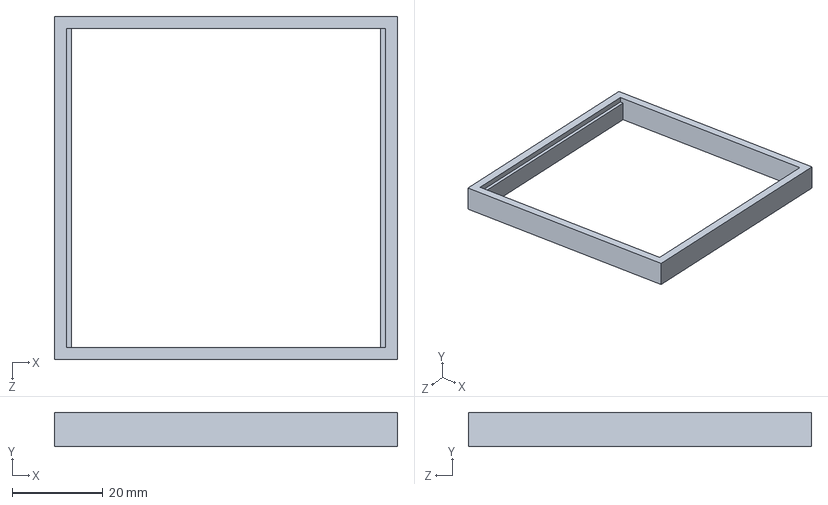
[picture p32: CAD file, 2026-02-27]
mechanical/stencil_supports/MainFlightComputer_support.SLDPRT
75.4 x 7.50 x 75.4 mm

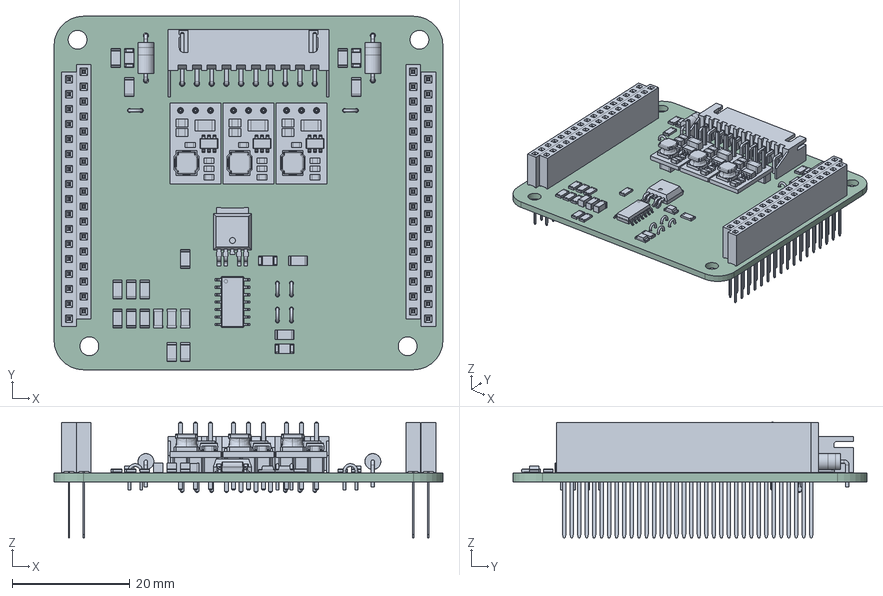
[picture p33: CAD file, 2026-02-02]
pcb/models/MainPowerDistributionSystem.step
66.0 x 60.0 x 19.6 mm
JST_XH_S10B-XH-A_1x10_P2.50mm_Horizontal
R_1206_3216Metric x 15
LED_1206_3216Metric x 4
TestPoint_Bridge_Pitch2.0mm_Drill0.7mm x 6
C_1206_3216Metric x 7
SOIC-14_3.9x8.7mm_P1.27mm
D_A-405_P7.62mm_Horizontal x 2
d24v7fx-step-down-voltage-regulators x 3
PinHeader_1x03_P2.54mm_Vertical x 3
StackingHeader_2.54mm_1x17 x 4
MainPowerDistributionSystem 1.47.1
MainPowerDistributionSystem_PCB

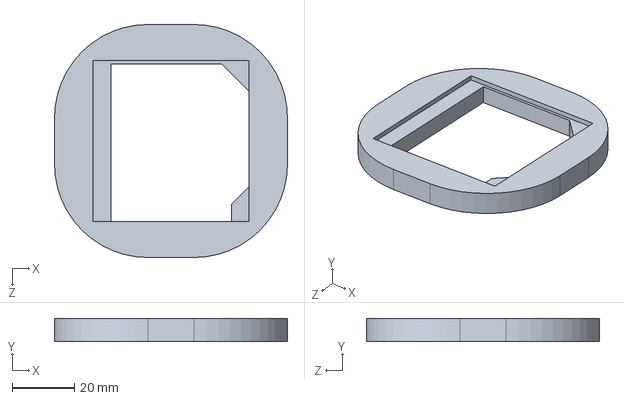
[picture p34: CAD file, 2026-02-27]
mechanical/stencil_supports/MainCameraSystem_support.SLDPRT
74.9 x 7.50 x 74.9 mm

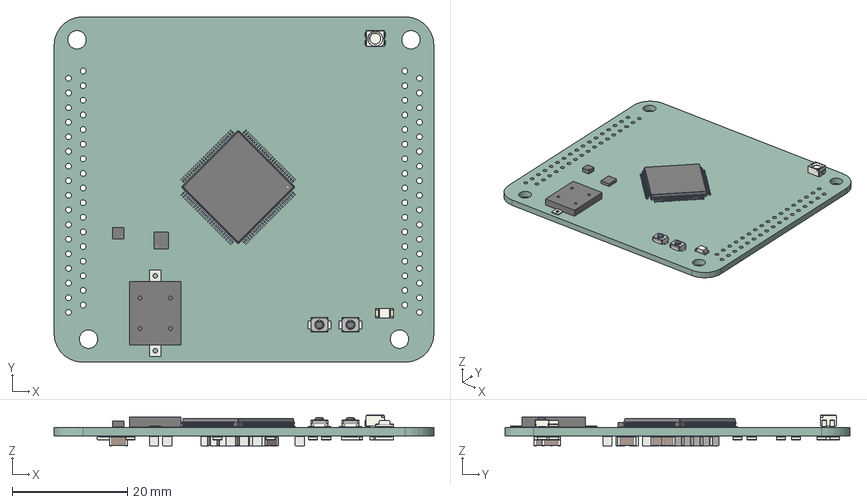
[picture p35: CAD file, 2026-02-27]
mechanical/stencil_supports/MainFlightComputer_R2_pcb.step
66.0 x 60.0 x 5.33 mm
LGA-12_2x2mm_P0.5mm
SW_SPST_B3U-1000P x 2
LED_1206_3216Metric
LED_RGB_Wuerth-PLCC4_3.2x2.8mm_150141M173100
LQFP-100_14x14mm_P0.5mm
Buzzer_Mallory_AST1109MLTRQ
LGA-14_3x2.5mm_P0.5mm_LayoutBorder3x4y
R_1206_3216Metric x 16
C_1206_3216Metric x 19
MainFlightComputer_R2_PCB

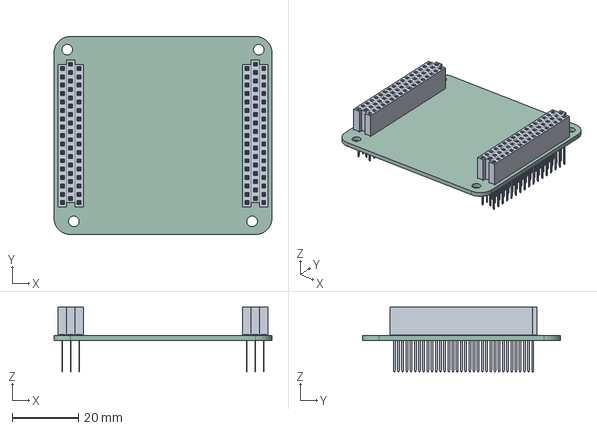
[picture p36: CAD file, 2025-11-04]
pcb/models/Main_Stack_Dummy.step
66.0 x 60.0 x 19.6 mm
StackingHeader_2.54mm_1x17 x 6
MainFlightComputer_PCB

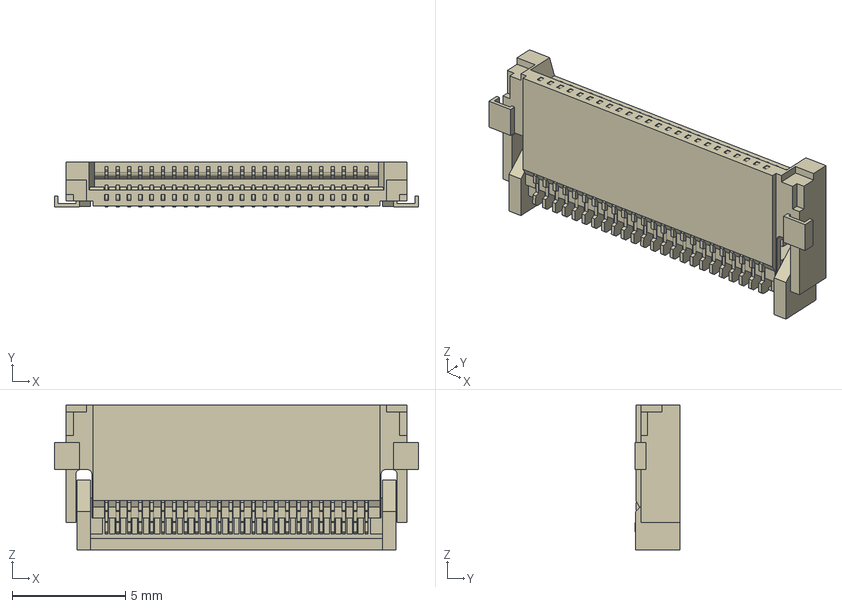
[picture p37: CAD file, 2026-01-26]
pcb/models/XF3M_2415_1B.stp
16.1 x 2.00 x 6.40 mm

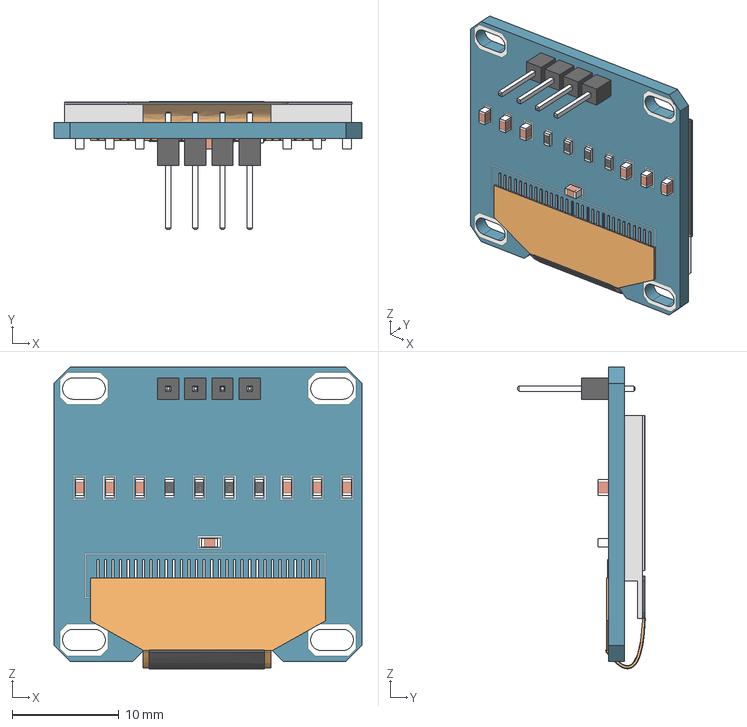
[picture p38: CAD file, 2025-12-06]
pcb/models/SSD1306_pin.stp
28.8 x 12.0 x 28.2 mm

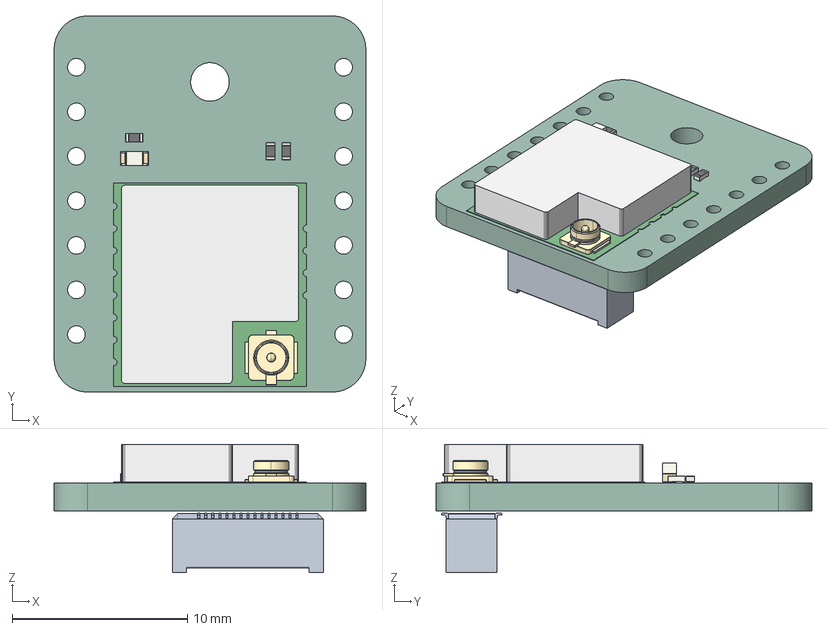
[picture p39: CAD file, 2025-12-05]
pcb/models/Wio-SX1262_for_XIAO_3D_file.step
17.8 x 21.4 x 7.30 mm
R_0402_1005Metric x 3
LED_0603_1608Metric
PCB
BF04-30pin-35H
Wio-SX1262 for XIAO V1.0_PCB

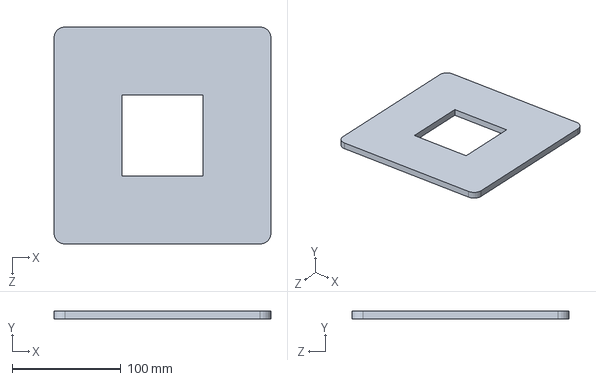
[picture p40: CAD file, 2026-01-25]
mechanical/stencil_supports/StencilSupportPlate.SLDPRT
200.0 x 7.50 x 200.0 mm

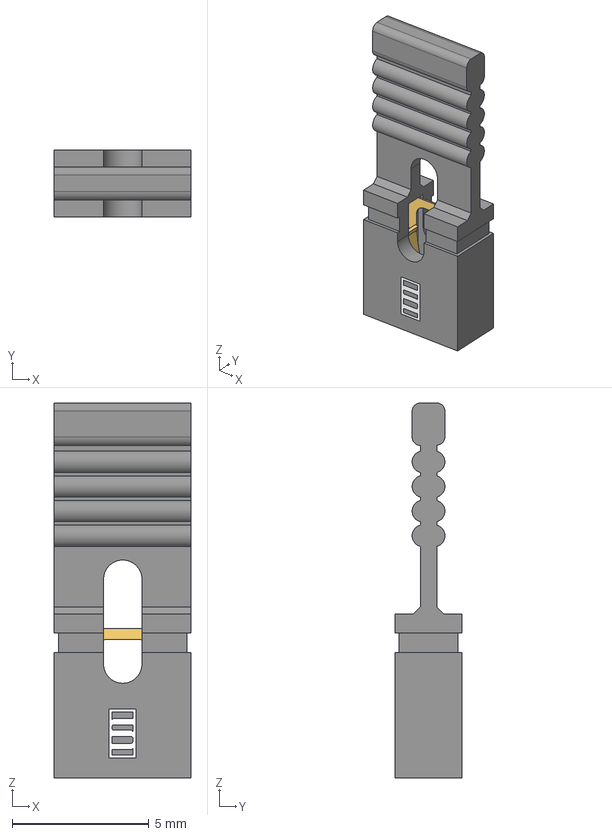
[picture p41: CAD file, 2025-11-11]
pcb/models/NPC02SXON-RC.step
5.00 x 2.44 x 13.7 mm
logo

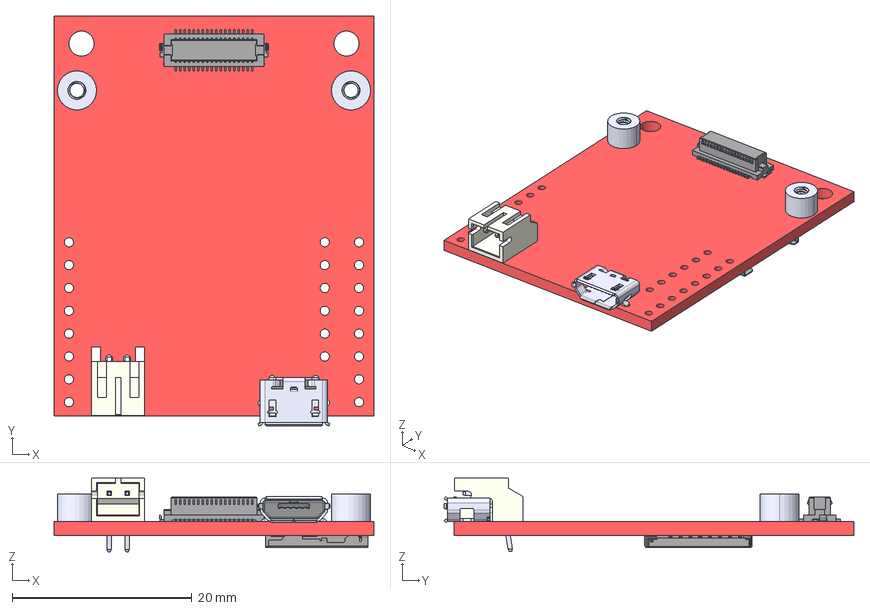
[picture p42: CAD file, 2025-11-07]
pcb/models/openmv_h7_plus_board.step
35.6 x 45.6 x 8.18 mm
1050170001 micro usb
1050170001 micro usb001
1050170001 micro usb002
1050170001 micro usb003
1050170001 micro usb004
1050170001 micro usb005
1050170001 micro usb006
1050170001 micro usb007
1050170001 micro usb008
1050170001 micro usb009
1050170001 micro usb010
1050170001 micro usb011
9774030243R-standoff x 2
DF12NB-36DS-0_5V.prt
S2B-PH-K-S(LF)(SN) jst
S2B-PH-K-S(LF)(SN) jst001
S2B-PH-K-S(LF)(SN) jst002

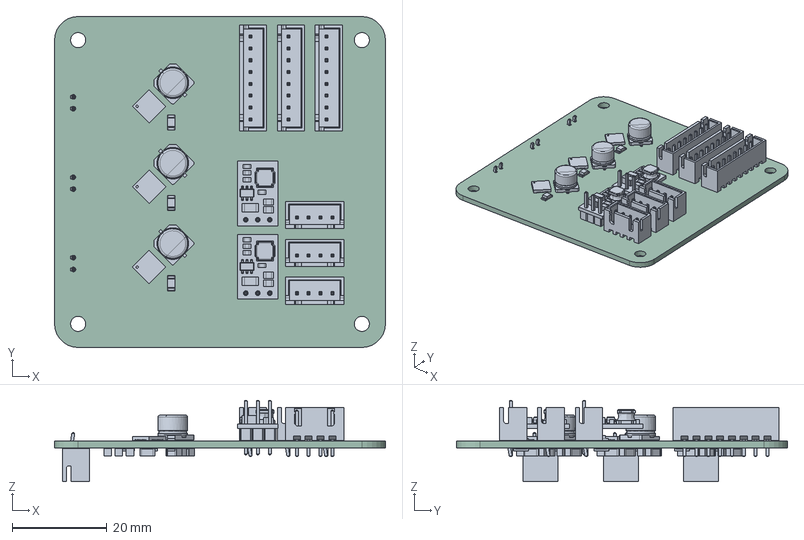
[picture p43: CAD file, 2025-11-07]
pcb/models/VehiclePowerDistributionSystem.step
70.0 x 70.0 x 17.2 mm
LED_1206_3216Metric x 3
JST_XH_B4B-XH-A_1x04_P2.50mm_Vertical x 3
Body_Solid1 x 3
Body001_Solid1 x 3
Array_Solid1 x 21
Array001_Solid2 x 18
Body002_Solid1 x 3
Array002_Solid1 x 21
Array003_Solid2 x 18
Body003_Solid1 x 3
Body004_Solid1 x 3
JST_XH_B8B-XH-A_1x08_P2.50mm_Vertical x 3
CP_Elec_6.3x5.4 x 3
d24v7fx-step-down-voltage-regulators x 2
PinHeader_1x03_P2.54mm_Vertical x 2
C_1206_3216Metric x 21
R_1206_3216Metric x 9
JST_XH_B2B-XH-A_1x02_P2.50mm_Vertical x 3
VehiclePowerDistributionSystem_PCB

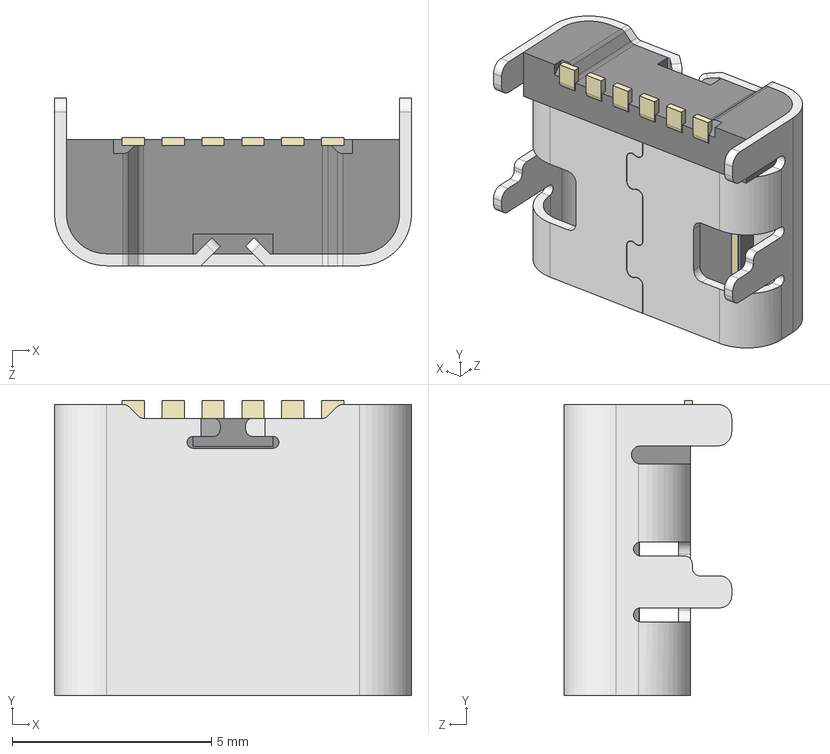
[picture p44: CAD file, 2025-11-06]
pcb/models/USB_C_Receptacle_HRO_TYPE-C-31-M-17.stp
8.95 x 7.40 x 4.20 mm

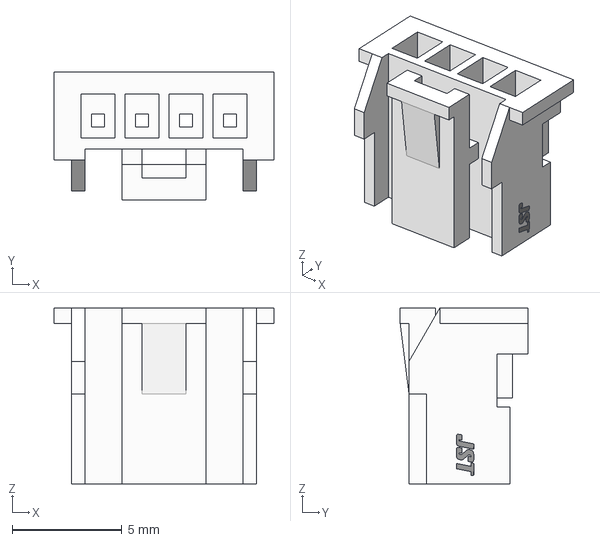
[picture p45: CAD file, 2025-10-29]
pcb/models/JST-PAP-04V-S.step
10.0 x 5.80 x 8.00 mm
PAP-04V-S
logo

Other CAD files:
mechanical/stencil_supports/VehicleFlightComputer_support.SLDPRT
mechanical/stencil_supports/VehiclePowerDistributionSystem_support.SLDPRT
pcb/models/S12B-PADSS-1.STEP
pcb/models/S04B-PASK-2.STEP
pcb/models/1.25mm_PicoBlade_Cable.stp
pcb/models/1.25mm_PicoBlade_Header.stp
pcb/models/ElectronicsBoxCase_AN-14F-01_Body.step
pcb/models/ElectronicsBoxCase_AN-14F-01_Lid.step
pcb/models/FFC2B28-24-G.step
pcb/models/IDC_40pin_cable.step
pcb/models/ItsyBitsy_ESP32.step
pcb/models/Micro_USB_Plug.step
pcb/models/Nucleo64_STLink_Debugger.step
pcb/models/Seeed_Studio_XIAO-ESP32-S3-Sense_Cameraless.step
pcb/models/StackingHeader_2.54mm_1x17.step
pcb/models/USB_Micro_Vertical.stp
pcb/models/VQFN-28-1EP_5x5mm_P0.5mm_EP3.7x3.7mm.STEP
pcb/models/d24v7fx-step-down-voltage-regulators.step
pcb/models/uSD_Connector_Molex.step
pcb/models/vn100_rugged.step

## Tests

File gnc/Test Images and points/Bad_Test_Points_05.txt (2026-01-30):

[(180, 0), (181, 5), (183, 10), (184, 15), (185, 20), (187, 25), (188, 30), (189, 35), (190, 40), (138, 45), (138, 50), (138, 55), (138, 60), (138, 65), (138, 70), (138, 75), (138, 80), (138, 85), (138, 90), (138, 95), (138, 100), (138, 105), (138, 110), (138, 115), (138, 120), (138, 125), (138, 130), (138, 135), (138, 140), (138, 145), (138, 150), (138, 155), (138, 160), (137, 165), (137, 170), (137, 175), (137, 180), (137, 185), (137, 190), (137, 195), (136, 200), (136, 205), (136, 210), (136, 215), (136, 220), (136, 225), (136, 230), (135, 235)]

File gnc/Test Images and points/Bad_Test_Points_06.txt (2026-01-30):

[(0, 29), (5, 40), (10, 43), (15, 49), (20, 57), (25, 57), (30, 75), (35, 75), (40, 6), (45, 96), (50, 103), (55, 101), (60, 114), (65, 114), (70, 126), (75, 132), (80, 137), (85, 143), (90, 150), (95, 153), (100, 161), (105, 169), (110, 172), (115, 174), (120, 179), (125, 188), (130, 196), (135, 199), (140, 203), (145, 205), (150, 212), (155, 216), (160, 219), (165, 226), (170, 233), (175, 234), (180, 239), (185, 239), (190, 239), (195, 239), (200, 239), (205, 239), (210, 239), (215, 239), (220, 239), (225, 239), (230, 239), (235, 239), (240, 239), (245, 239), (250, 239), (255, 239), (260, 239), (265, 239), (270, 239), (275, 239), (280, 239), (285, 239), (290, 239), (295, 239), (300, 239), (305, 239), (310, 239), (315, 239)]

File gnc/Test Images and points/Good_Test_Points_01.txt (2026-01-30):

[(135, 0), (135, 1), (135, 2), (135, 3), (135, 4), (182, 5), (182, 6), (182, 7), (182, 8), (183, 9), (183, 10), (183, 11), (183, 12), (184, 13), (184, 14), (184, 15), (184, 16), (185, 17), (185, 18), (185, 19), (186, 20), (186, 21), (186, 22), (186, 23), (187, 24), (187, 25), (187, 26), (188, 27), (188, 28), (188, 29), (188, 30), (188, 31), (189, 32), (189, 33), (189, 34), (189, 35), (189, 36), (189, 37), (136, 38), (136, 39), (136, 40), (136, 41), (136, 42), (136, 43), (136, 44), (136, 45), (136, 46), (136, 47), (136, 48), (136, 49), (136, 50), (136, 51), (136, 52), (136, 53), (136, 54), (136, 55), (136, 56), (136, 57), (136, 58), (136, 59), (136, 60), (136, 61), (136, 62), (136, 63), (136, 64), (136, 65), (136, 66), (136, 67), (136, 68), (136, 69), (136, 70), (136, 71), (136, 72), (136, 73), (136, 74), (136, 75), (136, 76), (136, 77), (136, 78), (136, 79), (136, 80), (136, 81), (136, 82), (136, 83), (136, 84), (136, 85), (136, 86), (136, 87), (136, 88), (136, 89), (136, 90), (136, 91), (136, 92), (136, 93), (136, 94), (136, 95), (136, 96), (136, 97), (136, 98), (136, 99), (136, 100), (136, 101), (136, 102), (136, 103), (136, 104), (136, 105), (136, 106), (136, 107), (136, 108), (136, 109), (136, 110), (136, 111), (136, 112), (136, 113), (136, 114), (136, 115), (136, 116), (136, 117), (136, 118), (136, 119), (136, 120), (136, 121), (136, 122), (136, 123), (136, 124), (136, 125), (136, 126), (136, 127), (136, 128), (136, 129), (136, 130), (136, 131), (136, 132), (136, 133), (136, 134), (136, 135), (136, 136), (135, 137), (135, 138), (135, 139), (135, 140), (135, 141), (135, 142), (135, 143), (135, 144), (135, 145), (135, 146), (135, 147), (135, 148), (135, 149), (135, 150), (135, 151), (135, 152), (135, 153), (135, 154), (135, 155), (135, 156), (135, 157), (135, 158), (135, 159), (135, 160), (135, 161), (135, 162), (135, 163), (135, 164), (135, 165), (135, 166), (135, 167), (135, 168), (135, 169), (135, 170), (135, 171), (135, 172), (135, 173), (135, 174), (135, 175), (135, 176), (135, 177), (135, 178), (135, 179), (135, 180), (135, 181), (125, 182), (125, 183), (126, 184), (126, 185), (134, 186), (134, 187), (134, 188), (134, 189), (134, 190), (134, 191), (134, 192), (134, 193), (134, 194), (134, 195), (134, 196), (134, 197), (134, 198), (134, 199), (134, 200), (134, 201), (134, 202), (134, 203), (134, 204), (134, 205), (134, 206), (134, 207), (134, 208), (134, 209), (134, 210), (134, 211), (133, 212), (133, 213), (133, 214), (133, 215), (133, 216), (133, 217), (133, 218), (133, 219), (133, 220), (133, 221), (133, 222), (133, 223), (133, 224), (133, 225), (133, 226), (133, 227), (133, 228), (133, 229), (133, 230), (133, 231), (133, 232), (133, 233), (133, 234), (132, 235), (132, 236), (133, 237), (133, 238), (133, 239)]

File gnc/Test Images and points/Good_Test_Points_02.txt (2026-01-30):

[(0, 72), (1, 72), (2, 72), (3, 72), (4, 72), (5, 72), (6, 72), (7, 72), (8, 72), (9, 72), (10, 71), (11, 71), (12, 71), (13, 71), (14, 70), (15, 70), (16, 70), (17, 69), (18, 69), (19, 69), (20, 69), (21, 69), (22, 69), (23, 69), (24, 68), (25, 68), (26, 68), (27, 68), (28, 68), (29, 67), (30, 67), (31, 67), (32, 67), (33, 67), (34, 66), (35, 66), (36, 66), (37, 66), (38, 66), (39, 66), (40, 66), (41, 65), (42, 65), (43, 65), (44, 65), (45, 65), (46, 65), (47, 64), (48, 64), (49, 64), (50, 64), (51, 64), (52, 64), (53, 63), (54, 63), (55, 63), (56, 63), (57, 63), (58, 63), (59, 62), (60, 62), (61, 62), (62, 62), (63, 62), (64, 62), (65, 62), (66, 62), (67, 62), (68, 61), (69, 61), (70, 61), (71, 61), (72, 61), (73, 60), (74, 60), (75, 60), (76, 60), (77, 60), (78, 60), (79, 59), (80, 59), (81, 59), (82, 59), (83, 59), (84, 59), (85, 59), (86, 59), (87, 59), (88, 59), (89, 59), (90, 59), (91, 58), (92, 58), (93, 58), (94, 58), (95, 58), (96, 58), (97, 58), (98, 57), (99, 57), (100, 57), (101, 57), (102, 57), (103, 57), (104, 57), (105, 57), (106, 57), (107, 56), (108, 56), (109, 56), (110, 56), (111, 56), (112, 56), (113, 56), (114, 56), (115, 56), (116, 56), (117, 56), (118, 56), (119, 55), (120, 55), (121, 55), (122, 55), (123, 55), (124, 55), (125, 55), (126, 55), (127, 55), (128, 55), (129, 55), (130, 55), (131, 54), (132, 54), (133, 54), (134, 54), (135, 54), (136, 54), (137, 54), (138, 54), (139, 54), (140, 54), (141, 54), (142, 54), (143, 54), (144, 53), (145, 53), (146, 53), (147, 53), (148, 53), (149, 53), (150, 53), (151, 53), (152, 53), (153, 53), (154, 53), (155, 53), (156, 53), (157, 53), (158, 53), (159, 53), (160, 53), (161, 53), (162, 53), (163, 53), (164, 53), (165, 53), (166, 53), (167, 53), (168, 53), (169, 53), (170, 52), (171, 52), (172, 52), (173, 52), (174, 52), (175, 52), (176, 52), (177, 52), (178, 52), (179, 52), (180, 52), (181, 52), (182, 52), (183, 52), (184, 52), (185, 52), (186, 52), (187, 52), (188, 52), (189, 52), (190, 52), (191, 52), (192, 52), (193, 52), (194, 52), (195, 52), (196, 52), (197, 52), (198, 52), (199, 52), (200, 52), (201, 52), (202, 52), (203, 52), (204, 52), (205, 52), (206, 52), (207, 52), (208, 52), (209, 52), (210, 52), (211, 52), (212, 52), (213, 52), (214, 52), (215, 52), (216, 52), (217, 52), (218, 52), (219, 52), (220, 52), (221, 52), (222, 52), (223, 52), (224, 52), (225, 52), (226, 52), (227, 52), (228, 52), (229, 52), (230, 52), (231, 52), (232, 52), (233, 52), (234, 53), (235, 53), (236, 53), (237, 53), (238, 53), (239, 53), (240, 53), (241, 53), (242, 53), (243, 53), (244, 53), (245, 53), (246, 53), (247, 53), (248, 53), (249, 54), (250, 54), (251, 53), (252, 53), (253, 53), (254, 53), (255, 53), (256, 54), (257, 54), (258, 54), (259, 54), (260, 54), (261, 54), (262, 54), (263, 54), (264, 54), (265, 54), (266, 54), (267, 54), (268, 54), (269, 54), (270, 54), (271, 54), (272, 55), (273, 55), (274, 55), (275, 55), (276, 55), (277, 55), (278, 55), (279, 55), (280, 55), (281, 55), (282, 55), (283, 55), (284, 55), (285, 55), (286, 55), (287, 56), (288, 56), (289, 56), (290, 56), (291, 56), (292, 56), (293, 57), (294, 57), (295, 57), (296, 57), (297, 57), (298, 57), (299, 57), (300, 57), (301, 57), (302, 57), (303, 57), (304, 58), (305, 58), (306, 58), (307, 58), (308, 58), (309, 58), (310, 58), (311, 58), (312, 58), (313, 58), (314, 58), (315, 58), (316, 58), (317, 59), (318, 59), (319, 59)]

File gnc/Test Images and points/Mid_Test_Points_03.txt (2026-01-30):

[(118, 63), (118, 66), (118, 69), (118, 72), (118, 75), (118, 78), (118, 81), (118, 84), (118, 87), (118, 90), (118, 93), (117, 96), (117, 99), (117, 102), (117, 105), (117, 108), (117, 111), (117, 114), (117, 117), (117, 120), (117, 123), (117, 126), (117, 129), (117, 132), (117, 135), (117, 138), (117, 141), (117, 144), (117, 147), (117, 150), (116, 153), (116, 156), (116, 159), (116, 162), (116, 165), (116, 168), (116, 171), (116, 174), (115, 177), (115, 180), (115, 183), (115, 186), (115, 189), (115, 192), (115, 195), (115, 198), (114, 201), (114, 204), (114, 207), (114, 210), (114, 213), (114, 216), (114, 219), (113, 222), (113, 225), (113, 228), (113, 231), (113, 234), (113, 237)]

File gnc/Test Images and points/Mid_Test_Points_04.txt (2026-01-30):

[(0, 86), (3, 86), (6, 85), (9, 85), (12, 85), (15, 84), (18, 84), (21, 84), (24, 83), (27, 83), (30, 83), (33, 83), (36, 82), (39, 82), (42, 82), (45, 82), (48, 81), (51, 81), (54, 81), (57, 80), (60, 80), (63, 80), (66, 80), (69, 80), (72, 80), (75, 79), (78, 79), (81, 79), (84, 79), (87, 79), (90, 79), (93, 79), (96, 79), (99, 79), (102, 78), (105, 78), (108, 78), (111, 78), (114, 78), (117, 78), (120, 78), (123, 78), (126, 78), (129, 78), (132, 77), (135, 77), (138, 77), (141, 77), (144, 78), (147, 78), (150, 78), (153, 78), (156, 78), (159, 78), (162, 78), (165, 78), (168, 78), (171, 78), (174, 78), (177, 78), (180, 78), (183, 79), (186, 79), (189, 79), (192, 79), (195, 79), (198, 80), (201, 80), (204, 80), (207, 81), (210, 81), (213, 81), (216, 81), (219, 81), (222, 82), (225, 82), (228, 82), (231, 83), (234, 83), (237, 83), (240, 83), (243, 84), (246, 84), (249, 84), (252, 85), (255, 85), (258, 85), (261, 86), (264, 24), (267, 25), (270, 27), (273, 29), (276, 31), (279, 33), (282, 35), (285, 41), (288, 90), (291, 90), (294, 91), (297, 91), (300, 92), (303, 92), (306, 92), (309, 93), (312, 94), (315, 94), (318, 95)]

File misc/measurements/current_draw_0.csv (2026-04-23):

#Digilent WaveForms Oscilloscope Acquisition
#Device Name: Discovery3
#Serial Number: SN:210415B99EB7
#Date Time: 2026-04-22 16:59:15.766.158.250
#Sample rate: 606.815Hz
#Samples: 16000
#Trigger: Source: Channel 1 Type: Edge Condition: Rising Level: 600 mV Hyst.: Auto HoldOff: 0 s
#Math 1: Function: C1 / 1.2
#Everything except VN-100.
Time (s) | Math 1 (A)
-13.1836 | 0.0009129657172961391
-13.18195205 | 0.001662579222564039
-13.1803041 | 0.001662579222564039
-13.17865615 | 0.001662579222564039
-13.1770082 | 0.003161806233098474
-13.17536025 | 0.005410646748901608
-13.1737123 | 0.006160260254168826
-13.17206435 | 0.006909873759436044
-13.1704164 | 0.006909873759436044
-13.16876845 | 0.00466103324363291
-13.1671205 | 0.00466103324363291
-13.16547255 | 0.00466103324363291
-13.1638246 | 0.003911419738365693
-13.16217665 | 0.002412192727831257
-13.1605287 | 0.003161806233099838
-13.15888075 | 0.00466103324363291
-13.1572328 | 0.003911419738365693
-13.15558485 | 0.004661033243632228
-13.1539369 | 0.003911419738365693
-13.15228895 | 0.003911419738365693
-13.150641 | 0.003911419738365693
-13.14899305 | 0.00466103324363291
-13.1473451 | 0.00466103324363291
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

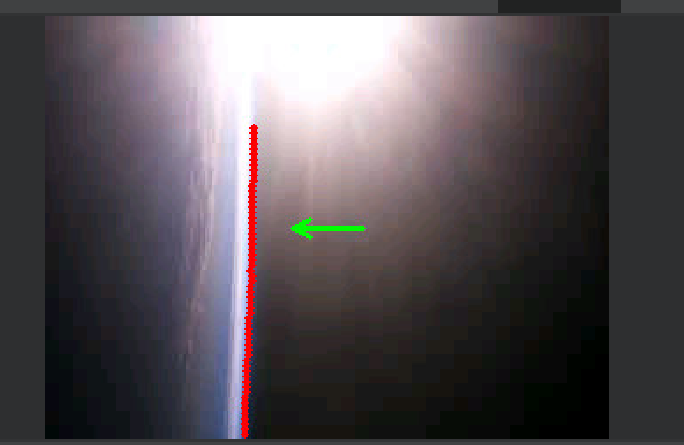
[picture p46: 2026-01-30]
gnc/Test Images and points/Mid_Test_Image_03.png

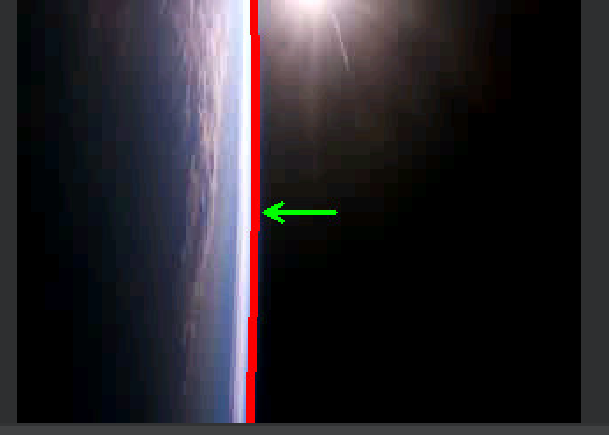
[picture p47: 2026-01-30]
gnc/Test Images and points/Good_Test_Image_01.png

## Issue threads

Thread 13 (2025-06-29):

What PCB manufacturer will we be using?

RalphManchester, 2025-06-29:
I'd like to know the capabilities of the manufacturer we'll be using to make our PCBs.

PhucXDoan, 2025-06-29:
For 2024-2025, we used PCBWay, but we might be using JLCPCB if its cheaper.

As for capabilities, I might make a document of minimum trace widths, via aspect ratio requirements, etc. as a reference at some point. I'll give an update on that when I can (and if I remember).

Closed 2025-06-29.

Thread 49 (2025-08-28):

First version of the camera subsystem PCB.

PhucXDoan, 2025-08-28:
For the 2024-2025 year, we used an [OV5640 breakout board by Adafruit](https://www.adafruit.com/product/5673?srsltid=AfmBOopl7l1nZpbgTdDv-7UmoZb66t6NSTfeFxZ1wCI_X42blO4-yosq), which worked, but the main challenge with it was the fact that we had to deal with the 18 pins; since the camera MCU that was driving the OV5640 was in the electronics box, there was a lot of pressure on the pin-out count.

Instead of using [MIPI-CSI](https://en.wikipedia.org/wiki/Camera_Serial_Interface), we could "instead" use a camera module that had a SPI, I2C, etc. interface, and this will reduce the amount of data lines needed, but this will also absolutely kill data throughput (8-bit bus vs. 1-bit bus).

Furthermore, any OV5640 camera module out there that had a SPI output would actually just be a board with an MCU that talked with the OV5640 directly via MIPI-CSI and then spit out the data using SPI.

So let's just _**cut the middle man out**_ and make a PCB with a microcontroller that can drive an OV5640 and save image data directly to an uSD!

Thus, the camera subsystem PCB will will have three main parts:

1. Flexible-flat-cable connector for the OV5640 (or otherwise compatible) camera.
2. An STM32H533VET6 to drive the camera.
3. Another plug-connector for the uSD; the uSD itself will be in the electronics box, so we'll route wires from this connector to the electronics box's connector.

For those who likes to look at the pictures more than words in books:

<p align="center"><kbd>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</kbd></p>&nbsp;

If we design this well, then the camera subsystem will be very modular as it is completely independent from the other subsystems. All we need to do is just supply power and the MCU should just immediately start saving image data.

If we put mounting holes at strategic spots, we can give the mechanical team lots of leeway in how to place the PCB and where to position the camera module (with a long ribbon connector, we can have lots of flexibility too).

The PCB should also have a log of debug functionalities to it; as of writing, here are some that come to my mind:

1. Lots of status LEDs.
2. Reset button (enabled with a pin-jumper).
3. An uSD connector on the PCB itself; we wouldn't be using this in production, but it'd be convenient to have.
4. Buzzer.
5. A USB-UART bridge port.

There's a lot we have to do first before we can get close to finalizing the PCB, but this should be a good "demo" of how we'll design the other PCBs.

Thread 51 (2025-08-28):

SPI driver for STM32H533.

PhucXDoan, 2025-08-28:
We're doing things quite low-level and bare-metal, so there's no ST HAL here to help us to set up the SPI peripheral; we're going to have to do it ourselves!

If you're new to STM32 programming (and even if you are, but never worked directly with registers before), then here are some tips that first come to my mind:

1. RTFM! The [reference manual](https://www.st.com/resource/en/reference_manual/rm0481-stm32h52333xx-stm32h56263xx-and-stm32h573xx-armbased-32bit-mcus-stmicroelectronics.pdf) (and at times, the data sheet) is _**THE THING THAT HAS ALL THE ANSWERS!**_ Read up on the SPI section thoroughly.
2. First figure out how the SPI peripheral that you're using is clocked; this doesn't mean the clock rate of the SPI's CLK, but rather at what frequency *the SPI hardware itself is running at*. See the top-level clock-tree in the RM to learn more.
3. Oh yeah, before you even do anything, figure out which SPI peripheral you're using at all. See the CSV file in `deps/mcu/` which has all of the GPIOs of the MCU and what their capabilities are. You can open this file in Excel or whatever, but this file was also generated by STM32CubeMX, so if you already have that installed, you can load the MCU in that and see what options you have for SPI. To know where the SPI pins are on the Nucleo board itself, I suggest you to download the CAD files of the [Nucleo board's PCB](https://www.st.com/en/evaluation-tools/nucleo-h533re.html#cad-resources) and open it in KiCad. From there, just go to the MCU's pin and follow where it goes to the Morpho connectors.
4. There are A LOT of [subtleties and gotchas](http://efton.sk/STM32/gotcha/index.html) to the kind of programming we're doing, but that's OK. I'm knowledgeable about these systems, so just ASK!

The first draft of the SPI driver should be something like this:

1. Have an initialization procedure to initialize the SPI peripheral.
2. Have a blocking procedure for the master to send data and (optionally) receive data from the slave.

That should be the whole API. Nothing more complicated, please.

Later on, we'll probably need to improve the performance of the SPI driver to use things like DMA and what not, but let's just start with getting something working!

PhucXDoan, 2025-08-30:
[Here is the implementation of the SPI for the 2024-2025 year.](https://github.com/RockSat-X/2025/blob/main/CameraSystem/spicomms.c)

The development environment has _**changed a lot**_ since then, so take things with a grain of salt there.

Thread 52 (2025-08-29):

I2C driver for STM32H533.

PhucXDoan, 2025-08-29:
See the issue for making a [SPI driver on the STM32H533](https://github.com/RockSat-X/RSXVT2026/issues/51).

The main difference with the I2C driver over the SPI driver will be the amount of error handling. With SPI, the master has no idea whether or not the data stream is being received by the slave or if the slave is even synchronized with the master (although maybe a CRC or READY signal can help with this). For I2C, because the data and clock lines are half-duplex, the master can encounter a lot of issues, such as the slave not responding or if there's some weird bus contention going on.

Overall, however, the API should look relatively simple:

1. Initialization procedure to initialize the I2C peripheral.
2. Have a blocking procedure for the master to read and write to the slave.

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

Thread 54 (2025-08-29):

FAT file-system.

PhucXDoan, 2025-08-29:
There's two ways for the STM32H533 to communicate with the uSD: by using SPI or through SDMMC.

Regardless of how communication is done, read/writes to the uSD is done in chunks of 512-byte sectors.

By reading sectors of the uSD, the file-system of the uSD can be determined (e.g. FAT32, exFAT, NTFS, etc.) and then used to read/write entire files.

Of these file systems, we want to be using either FAT32 or exFAT; the former is old and has wide-spread support, but it limits files to 4 GiB. ExFAT is the modern replacement for FAT32 which removes this 4 GiB file limitation (and cleans a lot of cruft in the FAT32 specification).

I've written a basic FAT32 driver before; all it did was create a folder and dump binary data blobs in it. Ideally, this is all we need to do. We shouldn't have to be making a bunch of files in the file-system, because we can always do post-processing using a Python script to unpack the data later. Remember, reads/writes to the uSD are in chunks of 512-byte sectors, so it'd be stupid to write small amount of data at a time.

Although I have the FAT32 driver code still lying around, it's very janky and not to my bar of quality. I've started an exFAT driver, but never got to finish it, and if time permits, maybe I can finish it for this project.

Regardless, we can start off by using my beloved Elm-Chan's [FatFs](https://elm-chan.org/fsw/ff/) library to do this stuff for us; all we should need to do is provide the FatFs library with some basic routines to let it be able to query for sectors of the uSD and it'll handle the rest from there.

The FatFs library, however, is quite much more than what we need. It has to deal with directories and file names and whatever, but all we honestly need for this project is a way to dump data onto the uSD card. The fact that we're using a file-system at all is because it'll make mounting the card onto your machine and getting the data much easier. We could always do raw sector writes to the uSD and not have to deal with file-systems, but then the OS will see this as a "corrupt" drive. Besides, we want to be able to handle the situation of when there's several power-cycles and not accidentally overwrite any data already written to the card.

In terms of what we need to get done for this issue, it should be simple:

1. Procedure to initialize the uSD.
2. Procedure to initialize the file-system.
3. Procedure to dump 512 bytes worth of data.

That's it. We shouldn't be having to read file-data from the uSD to do things related to our project.

Closed 2025-10-03.

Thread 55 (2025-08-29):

How can we make debugging the STM32H533VET6 on the PCBs easy?

PhucXDoan, 2025-08-29:
As we get close to the part where we start having actual PCBs, we need to plan for ways to make the debugging experience of these boards as easy as possible. All PCBs with an STM32 MCU will have a SWD header (and some other stuff) so that the MCU can even be programmed.

But when we don't care about programming the MCU and just want the serial logs coming from it, we would still need to hassle with connecting up with the SWD header with an [ST-Link](https://www.adafruit.com/product/2548?srsltid=AfmBOooJ4wZtheqeyshCcDr4O3cLdXafBTymMC3385ApGAJVLPdwc9-cE_4) to get the UART data. Furthermore, if the PCB is locked away in the electronics box, we'll need to bring out the RX/TX lines, but we still need to play with the finicky RX/TX wires (and also ground) to get the serial data. Just overall bad UX.

One thing we can do is maybe use a USB-UART bridge like [MCP2221A](https://www.adafruit.com/product/4471?srsltid=AfmBOoqsNjiUbw0W5dhB1bOZde7AH6cKipoRheLlEfctqyLItdKRsEHk) or maybe the [CP2104(N)](https://learn.adafruit.com/adafruit-cp2102n-cp2104-friend-usb-to-serial-converter). Theoretically, all we need to do is plug in a USB cable and that's it! With this, we will have the advantage of the convenience of USB but not the hassle of writing an entire USB driver (I've done it, and I certainly do not have the time to do it again here on this project). Ideally, we place the USB-UART bridge somewhere easily accessible on the deck-plate.

But maybe not even that. Depending on the pin-count, we can bring the entire SWD header out of the electronics box and design a simple connector for it so we can almost plug-and-play with the ST-Link.

Lots of possibilities here!

PhucXDoan, 2025-08-29:
[Magnetic pogo pins](https://www.adafruit.com/product/5413) might be nice to use.

PhucXDoan, 2025-09-02:
This [ST-Link](https://www.adafruit.com/product/2548?srsltid=AfmBOoqz_7SCWuWaBP__vilnGe517WxF1AtcbNrx5qXDUZHYa3QBmVzd) and this [cable](https://www.adafruit.com/product/1675) seems compatible.

PhucXDoan, 2025-09-30:
The STLINK-V3MINIE does not actually supply power to the target unfortunately. I think this is common with most debuggers.

PhucXDoan, 2025-09-30:
If we use these [1.25mm pitched PicoBlade connector](https://www.digikey.com/en/products/detail/molex/0530471010/242861?s=N4IgTCBcDaIKwGYAMAWA7ARiVkBdAvkA) with this [cable](https://www.adafruit.com/product/4930?srsltid=AfmBOop5bDJ8VrNRZgDw1ZrIuwuYTEkldmztOCeH3QveIFaIWhlGYiJs), we can have a small footprint with enough pins for SWD (with SWO), power, and UART.

I think what we should then do is make a small PCB shield for the Nucleo-64 ST-Links so that we can use this custom debug cable easily.

PhucXDoan, 2025-10-04:
I think I've explored the space for LEDs, buzzers, SWO, and the USB-UART bridge enough that I can confidently say we will be in a much better position for having good debug tools even for the first revision of the PCBs.

Closed 2025-10-04.

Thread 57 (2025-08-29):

How should we do RF transmission?

PhucXDoan, 2025-08-29:
We need wireless communication between main and the vehicle; the vehicle will send sensor and image data back to the main electronics box so that we can (hopefully) recover it upon deintegration.

As of writing, my idea is to do the dumbest, simplest thing possible and just use an [ESP8266](https://www.adafruit.com/product/2471?srsltid=AfmBOorlEbe0qG78-xDZMUeX6KrnszpcuwmtBc7ogUfHz2mMv7yZnOke) so we can transmit over WiFi.

This approach has several advantages to be aware of:

1. _**It's easy to program.**_ As much as I don't like Arduino (or even the ESP for that matter), I doubt we have the capability to hand-roll something as complicated as the WiFi stack -- both hardware-wise and software-wise -- all in a single academic year.

2. _**It's easy to integrate.**_ The ESP8266 is just an all-in-one thing, so it should just be plug-and-play, and so we should be spending less time getting it to work. Furthermore, this also means it's easy to replace if anything were to happen.

3. _**Less crazy licensing.**_ With the ESP8266, it's just a WiFi device that's compliant with the regulation of FCC; the chances that it can be problematic will be slim. This doesn't mean we can skip the paperwork, however, but it will reduce the headache.

4. _**It's easy to do GPS rollout and RFI testing.**_ This I can not understate enough. If we have a more sophisticated RF system, then it needs to be designed to be verifiably working somehow. One of the tests that NASA does is GPS rollout and RFI testing where each university's experiment on the CarRoLL has their RF equipment (if any) enabled one at a time. This is so NASA can verify that the rocket's RF systems are not interfering with or by any experiment onboard.

Now what about the disadvantages?

1. _**We may need more transmission power.**_ We should design around a link of at least 100 meters, but whether or not the ESP8266 can handle this is not yet tested. Even if it was capable, this doesn't mean it'll perform the same in space with the other universities' experiments.

2. _**We may need higher throughput and reliability.**_ We need to transmit both sensor and image data, and the poor little ESP8266 might be able to handle it, especially if we roll up our sleeves and do some crazy data-compression. Nonetheless, the exact transmission speed we can get is an unknown, and there's a small chance we're going have to scope-up or downgrade data quality.

3. _**It's lame**_. This one is just my personal opinion honestly. It'd be cool if we can have a more advanced RF system, but that'll take some smart minds to tinker at. Besides, anything more than the ESP8266 will mean more specialized components (costs go up) and specialized knowledge in how to work with the system (effort goes up for the other non-RF people).

Let's see what we can come up with here.

shelbyoVT, 2025-10-07:
I know I should have probably figured this out mid last week but I did the ESP32 installation for Arduino. The error I received was that the port was busy or doesn't exist. My cable is capable of data transfer. AI told me that my problem was that I needed a driver, reading the ESP32 it would be the CP2102. Is that accurate, and where should I download this driver from?

PhucXDoan, 2025-10-07:
> The error I received was that the port was busy or doesn't exist.

IIRC, I gave you these [ESP-WROOM-32 dev-modules](https://www.amazon.com/ESP-WROOM-32-Development-Microcontroller-Integrated-Compatible/dp/B08D5ZD528) and the [XIAO ESP32-S3](https://www.seeedstudio.com/XIAO-ESP32S3-p-5627.html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). Notice how both have a **Reset** button and a **Boot** button.

<p align="center"><kbd>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</kbd></p>&nbsp;

I think what you have to do is press the Boot button to put the ESP into a mode where it can be programmed (this is what the bootloader does). The Arduino IDE should allow you to flash from there, and after the upload, press the reset button.

I don't think the CP2102 driver is necessary, because I didn't have to set that up, but then again, you could have a very different Windows installation from mine.

Don't stress too much about this though; I told you flashing the ESPs would be the hardest part :p.

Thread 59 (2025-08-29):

How to do computer vision?

PhucXDoan, 2025-08-29:
The vehicle will need a camera and processor to do computer vision and track a predefined target.

There are many parts to this we need to consider:

1. What camera resolution should we go for? Is 640x480 good enough or do we need something bigger?
2. What FOV can we use and which is best? Narrower means more pixels for the target, but we might accidentally lose visual of the target more easily.
3. Should we use a visible-light camera or can we go infrared?
4. Can we have a polarized lens to reduce glare?
5. Will lens distortion be a big issue?
6. What kind of image processing do we need to do? Will it be a simple circle-fitting algorithm or something more advanced with training data required?
7. What are the real-time constraints? Do we need to have tracking data every second? half-second? 100ms?
8. Where will the target even be? Will it be on the deck-plate or be a second ejectable?

There are probably many other things we need to account for, but this list should be most of it.

As of writing, the current plan is to _**maybe**_ use the [OpenMV-H7](https://www.digikey.com/en/products/detail/seeed-technology-co-ltd/102991322/11506484) to do the CV. This offers several benefits, like ease of programming, testing, and integration. However, there are still the other unknowns we need to address, like what our target will be and how capable the OpenMV-H7 will be able to track it.

I'd like to really figure out a better solution here, especially since OpenMV-H7 stock is hard to come by at a cheap price. However, this is not my area of expertise, so we're going to need some smart brains on this one.

ryan9182, 2025-09-28:
I was thinking along the same lines. Something like a distinct pattern of reflective dots on the object that we can track although would also work. I'm a little concerned about how the reflective strips would behave with such a large amount of light. If we are to use reflective strips without washing out the camera or risking the light scattering there cannot be a lot of surface area. That's why I think small dots could work since they would scatter into larger dots and should still be pretty easy to track. This is just an assumption because of what I saw in the video from another experiment. This should be something we can easily test anyways.

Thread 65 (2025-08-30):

Making stencil support for PCBs.

PhucXDoan, 2025-08-30:
Once we finish designing the PCBs, we should then preemptively design some 3D prints that'll make the soldering process much easier and less time consuming.

The way we will assemble the boards will be to use a soldering stencil to put down solder-paste at the pads of SMD components.

<p align="center"><kbd>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</kbd></p>&nbsp;

This involves having the stencil be well-aligned to the PCB and also flat in order to prevent warping of the stencil. After we do one side of the PCB, we take the stencil off, carefully place the components, and then bake the PCB.

However, we still have the opposite side to take care of!

Using the stencil for the other side becomes much more difficult because the soldered components on the PCB will protrude out and make it annoying to balance the PCB on a flat surface for the stencil.

So to save time and frustration, we should make a 3D print support that can have the PCB slotted in and be able to have the stencil flushed against the PCB and the 3D print support. This will make aligning the stencil easier and us not having to worry about warping it.

<p align="center"><kbd>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</kbd></p>&nbsp;

The same 3D print support can also have another slot but for the other side of the PCB; on the side of the PCB with the now-soldered components, the 3D print will have holes that'd avoid the components, but would otherwise support the PCB to be flush against the support's surface.

This should overall make the soldering process easier with the stencils.

Someone on mechanical with good CAD and 3D printing experience can pick up on this easily. A 3D step model can be rendered for each PCB as needed.

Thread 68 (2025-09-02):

Summer testing preparations.

PhucXDoan, 2025-09-02:
We should prepare the following things for when we bring our experiment to Wallops Flight Facility for testing and integration:

- Inventory sheet.
- Timeline spread-sheet of expected timer events, current draw, indicators, etc.
- Procedure check-sheets for Remove-Before-Flight, lock-tight applications, and such.

We'd at this point have done a full walk-around inspection of the experiment and briefed the people going to WFF on how exactly the testing is done there.

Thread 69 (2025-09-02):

Final vibration testing.

PhucXDoan, 2025-09-02:
Once all of the subsystems have been integrated onto the final deck-plate, we ought to perform some sort of vibration test to ensure the experiment will survive launch.

The specifications of the vibration test will be posted here once the new RockSat user-guide has been uploaded (and I remember to do so).

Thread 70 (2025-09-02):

Final full sequence test.

PhucXDoan, 2025-09-02:
The RockSat program will require us to put our experiment through several rounds of sequence testing to ensure that our experiment will behave as expected at each stage of the rocket flight.

One of the sequence tests we should be aware of is the *lightning test*, where we assume lighting struck near the launchpad and the rocket ends up blasting off.

The main implication of this test is that we won't get GSE before our TE lines.

So to ensure reliability, we shouldn't be designing our experiment assuming that GSE is guaranteed.

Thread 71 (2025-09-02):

Stickers/tags/markings for each inhibit and indicator.

PhucXDoan, 2025-09-02:
Our experiment implementation should be visibly well-documented.

Rather than have screw-switches, RBF pins, and LED indicators all on their own, we should look into seeing ways of documenting their purpose and meaning on the deck-plate using stickers, tags, markings, etc.

This will greatly aid summer testing and integration.

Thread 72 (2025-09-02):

Choice of batteries.

PhucXDoan, 2025-09-02:
We need to see what batteries we should be using for this year.

We can use the same batteries as we did for the 2024-2025 year, but there were some confusing issues with the UL requirements that took longer than expected to resolve. We shouldn't have the same issue again, but I'll have to look into that more.

We do not need the batteries to be rechargable; just last long enough on idle (let's say a month) and to power the ejectable(s) when it's launch time.

PhucXDoan, 2025-09-16:
We need to consider the desired battery voltage on the vehicle.

If 12V stepper motors are used, we'd need a good 12V supply to drive those motors.

A voltage boosting circuit could be used, but this might introduce a lot of noise, which will affect the sensors onboard.

PhucXDoan, 2025-10-06:
The batteries that were used last year are from EEMB.

It's also we actually look into seeing if we can design a rechargable vehicle (as in, the batteries can be kept in the vehicle and we can charge it with some exposed pins). For this, we need to look into proper UL listed chargers. It's likely we should look into having a UL charger circuit; making our own will be too risky.

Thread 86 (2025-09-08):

Integrating MCP2221A.

PhucXDoan, 2025-09-08:
Let's look into using a USB-UART bridge so we can use a USB cable to get serial data easily.

- [Adafruit breakout board](https://www.adafruit.com/product/4471?srsltid=AfmBOoqsNjiUbw0W5dhB1bOZde7AH6cKipoRheLlEfctqyLItdKRsEHk).
- [Datasheet](https://ww1.microchip.com/downloads/en/DeviceDoc/20005565C.pdf).
- [DigiKey](https://www.digikey.com/en/products/detail/microchip-technology/MCP2221AT-I-ST/6005338).
- [USB device port](https://www.digikey.com/en/products/detail/amphenol-cs-fci/10118192-0002LF/6817756).

A KiCad schematic can be made to plan out how to route up the MCP2221A.

I'm thinking of using a micro-USB port because it should be simpler to solder; maybe we can USB-C, but that might be more complicated than we need it to be.

Closed 2025-10-04.

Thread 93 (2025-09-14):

Standardized components and values.

PhucXDoan, 2025-09-14:
We need to document a standardized set of mechanical parts to use.

For instance, a common mounting hole size (e.g. M3) so the avionics and mechanical team avoid a mismatch like last year.

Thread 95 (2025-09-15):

OpenMV camera mount and stage.

PhucXDoan, 2025-09-15:
It'll be nice to have some sort of 3D printed mount and stage for the [OpenMV camera](https://openmv.io/products/openmv-cam-h7?srsltid=AfmBOoqM5nwIJ5TLbuWj4wxfHEI8B8ZFs2JfcGg2BLA1Bn8bCZ52xdOM) so we can easily test the camera against a flat background.

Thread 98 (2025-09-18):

Conversion of Timer Event signal into 3.3V logic for MCU.

PhucXDoan, 2025-09-18:
Last year, we used a simple Zener diode design to convert the high voltage of the TE lines into something safer for the MCU to read as a digital signal.

This is the schematic of it for last year:

<p align="center"><kbd>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</kbd></p>&nbsp;

This design had some issues (all to the fault of my own) and required a hacky fix.

What the issue was and what I did to fix it... I will actually not say.

This is so that I can make this be a learning opportunity for the issue assignees.

Thus the goal is this:
- What's wrong with the circuit?
- How can we fix it?

Of course, this Zener diode design is not the only way to approach the problem of converting high voltage to a lower one; if someone can come up with something better, that'll be great too.

PhucXDoan, 2025-10-02:
I know for the workshop we went through the whole spiel about using a voltage divider and then patching it up using a zener diode, but something I was thinking during that (and should've expressed) was that we probably don't need the resistor parallel to the diode, and my little research shows that this is indeed the case. So I played with Falstad a bit more:

<p align="center"><kbd>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</kbd></p>&nbsp;

So yeah, we kinda went full circle and probably going to end up with something very similar to last year :P. But worry not, I think it was a good exercise to start thinking like an engineer!

I think a 100 kilo-ohm resistor is good enough for the CMOZ3L3-TR-PBFREE, and this might also be fine for the 1N4728A zener diodes I'll give you tomorrow. Overall, I'll just let you experiment and figure it out.

In the end, look into drawing up a schematic in KiCad of the voltage converter circuit. We still need to put an LED somewhere, so think about whether we should have it be parallel to the entire voltage converter or have it be parallel to the zener diode instead.

Again, these design decisions are all up to you! Just experiment around with building circuits and playing with KiCad. The conversion of 28V to 3.3V won't be really that important until we do sequence testing in the second semester.

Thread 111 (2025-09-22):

Evaluating capabilities and limitations of OpenMV H7.

PhucXDoan, 2025-09-22:
We need to evaluate and document the capabilities and limitations of the [OpenMV H7 camera](https://www.digikey.com/en/products/detail/seeed-technology-co-ltd/102991322/11506484).

This mostly means figuring out the different CV algorithms that the OpenMV library provide as examples already and determining how accurate they are.

For instance, one of the algorithms that can be run on the OpenMV H7 is circle-fitting where circular objects in the image can be located at a (X, Y) coordinate. This circle-fitting algorithm can be a little janky and imprecise, however, so we'll need to look into what exactly causes inaccuracies and how we can improve upon it.

There might be other CV algorithms besides circle-fitting that we can potentially use for tracking; if they seem promising, we can explore that too.

PhucXDoan, 2025-10-01:
I'm going to give a more detailed list of "deliverables" here.

For Manan, since he's the one that has the camera right now, try looking into these things:

- Determine all the supported image formats that the OpenMV H7 camera can export. This means JPEG vs. raw, resolution size, color space, etc.
- For each of these image formats, determine their approximate size in bytes. There might be a way to just take a picture and then print out the picture's file size, but you can also probably automate this a bit by iterating through all the possible image formats, taking a picture, and then saving them to a uSD. Note that some image formats are fixed-size (e.g raw) but others are compressed (JPEG) and will vary; be scientific and document a bit on that if you can.
- With the different image formats, how do they affect the field-of-vision, if at all? Ideally, we want the smallest FOV, because this means we'll track the target from a farther distance; a huge FOV combined with low resolution might make things difficult.
- How does the camera handle bright light sources and dark lighting conditions? What if we there is a light source that's changing in brightness slowly vs. rapidly? How does the camera change its exposure? Can we control the camera's exposure level through code, or is it fixed by the hardware?

For people without the camera, meaning @ryan9182 and @justinvivadelli, here's some stuff we should look into:

- What are the available OpenMV cameras we could use? I know there's the OpenMV H7 and OpenMV H7 *Plus*, but to be honest, I have no idea what's the difference between them. I believe I gave Manan the original [OpenMV H7](https://www.digikey.com/en/products/detail/seeed-technology-co-ltd/102991322/11506484), but we need not use this exact model. If the board is red, it's probably compatible.
- Of the available cameras, which are practical to buy? The one I linked to DigiKey might be the only one we can actually by at a cheap price, because everything else is either out-of-stock or insanely marked up due to tariffs.
- What extension cables can we use? As of right now, the OpenMV H7 I gave to Manan has the camera mounted to the board, but if we want flexibility during integration, we should look into seeing if we can separate the camera from the board itself. I'm pretty sure the official OpenMV shop offers something, but I don't know how to use it.
- What different kinds of lenses can we use? As mentioned, we'd like a small FOV, so maybe a telescope lens is good to try out. I know there's also an IR lens, but I don't think it'll be that useful since there might be a lot of IR in space coming from the sun anyways (or maybe not? I'm spitballing there). We might end up just buying all the available lenses anyways, but it'll be nice to do some preliminary research here.
- Look into seeing if we can do some sort of simulation for the camera environment. For instance, I'm thinking it'll be really cool if we can create a Blender scene and be able to generate images that we can use to test the camera algorithms on (by loading on uSD card and having the OpenMV H7 parse and process them). Blender isn't that hard to learn the basics of, but I suspect doing good, realistic lighting to simulate the space conditions we might experience will be a bit of journey, but if someone is willing to put elbow grease into learning that, that'll be really cool.

Alright, that's everything on the top of my head right now. I'll comment more stuff if they come to me.

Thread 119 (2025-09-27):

ESP Range Test.

PhucXDoan, 2025-09-27:
We need to look into doing some range testing with the ESP modules.

If we can demonstrate that our simple WiFi RF system can work at 100 meters, that'll be more than enough for our experiment.

Of course, there'll be a lot of variables involved here that we'll need to consider. For instance, we might have a secondary experiment onboard that also have their own RF system going on, which may introduce some interference with our own RF system.

PhucXDoan, 2025-10-01:
Here's a more detailed description for this issue.

First, there's actually two kinds of ESPs we are looking into right now: ESP32 and ESP8266. From what I understand, the ESP8266 is a lesser version of the ESP32, but since all we need is basic data transmission over WiFi, perhaps the puny little ESP8266 is sufficient? Overall, the desirable properties for the RF system is it being long-range, fast, small, and cheap. @shelbyoVT, the ESPs I gave you last meeting are all ESP32s and I forgot to give you the [ESP8266](https://www.adafruit.com/product/2471?srsltid=AfmBOorKQ0yJgTjpuq3sHiqk5qy-p7PdqlFF7kP8lyeWbCTxPizmL8cQ), but I'll give you those too next time. I'd like for you to do a bit of research into these little guys and see what exactly are the differences between the ESP32 and ESP8266. The amount of programming should be pretty minimal; you get can get an LLM to do most of it for you if you really insist ¯\\\_(ツ)\_/¯.

Second, as mentioned, there are a lot of variables when it comes to doing the range test (between the ESP32 and ESP8266 that'll be provided to you):

- **Orientation** of the transmitter and receiver antennas.
- **Location**. I suggest doing this on the Drillfield or whatever large, open field there is. It's important to have a clear line-of-sight between the transmitter and receiver.
- **Time of day** (e.g. afternoon might result in more interference due to higher WiFi usage and thus shorter range?).
- **Weather**. I've heard WiFi frequencies get absorbed/reflected by water easily, so a humid day might imply worse range. Who knows?
- **Container**. I'm curious to see if by putting the receiver ESP in an aluminum electronics box how it'll affect the range. I'll provide you with the box when I can.

When you do your range test, you should try to document the independent variables:
- Which transmitter ESP was used.
- Which receiver EPS was used.
- Orientation of the ESPs.
- Place where the test was done.
- Time of day of the test.
- Weather conditions of the test.
- Whether or not an ESP was in an electronics box.

The dependent variable will be the maximum range until less than 90% of the packets are received (I just made this number up, just stop whenever things are starting to get inconsistent).

Overall, this is a lot, and I suspect this might take a while to do, but the main thing I want you to understand is that we should just be collecting as many data points as possible but not have it be exhaustive. For the deliverable, a big ol' spreadsheet with the things you tried and what you discovered is good enough. You can post your research here or on the GitHub Wiki.

Let me know if you have any questions.

PhucXDoan, 2025-10-06:
Another thing I came up with is RF interference testing.

We can have a bunch of ESPs grouped close together to see if it impacts the range at all.

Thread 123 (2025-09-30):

Nucleo-64 ST-Link shield.

PhucXDoan, 2025-09-30:
We should look into making a small shield for the Nucleo-64 ST-Link (the detachable part of the Nucleo board) that'll get the SWD pins, USB power, and UART TX/RX lines into a common connector.

The shield will mostly be a mechanical thing, so pretty much no electronics I'm imagining.

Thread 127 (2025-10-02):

Exploring the capabilities of the MCP2221A.

PhucXDoan, 2025-10-02:
The [MCP2221A](https://www.adafruit.com/product/4471?srsltid=AfmBOorizD0J26VSUe3Ty_y_b1nNFKPW-scDO3hUi1P4oqACjjvkLC8o) will be used as a bridge between the MCU on the PCB and the host computer for transmitting serial data just using a USB cable and a UART interface. In other words, rather than having to write a USB driver on the MCU, we can just use UART and this chip will do all the hard work for us to interface with our computers over USB.

It also seems like the MCP2221A has a bunch of other features too, like I2C and GPIOs. I don't think we'll need all these things, but it could be nice to have in the back of our minds if we know how they work.

So @JordanVXC, I'll provide you with the breakout boards and -- in your free time -- read the datasheet of the MCP2221A and play a bit with the chip. Just do some experiments and document stuff so we can reference it and maybe integrate it into our PCB designs.

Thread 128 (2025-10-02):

Test-points for uSD connector.

PhucXDoan, 2025-10-02:
Test-points on the bus lines of the uSD card connector is needed so we can determine if there's any impedance mismatch. To do this, we just need to put in some test-point symbols to the schematic at the right places. As of writing, here's what the schematic for the uSD card connector in `MainFlightComputer.kicad_sch` looks right now:

<p align="center"><kbd>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</kbd></p>&nbsp;

The footprint for the test-points should be the smallest available SMT pad there is.

Note that I could do this myself, but I'm making this issue ticket as something someone else can pick up and use as a way to practice KiCad.

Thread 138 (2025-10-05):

Functional Block Diagrams

lanaero, 2025-10-05:
- [ ] Create FBDs for entire system
- [ ] Determine electrical and physical inhibits
- [ ] Create subsystem hardware and software FBDs for FC, CVT, GNC

These must be descriptive. Refer to 2025 ISTR FBDs.

PhucXDoan, 2025-10-05:
Worked a bit on the FBD:

<p align="center"><kbd>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</kbd></p>&nbsp;

Some questions:

- Should there be an inhibit for the vehicle's stepper motors?
- What are the exact sensors that are being used on the main and vehicle side?
- What will go on in the ejection mechanism? I'm guessing burn wire, but is there anything else?
- There'll be two STM32H533VET6 MCUs in the main electronics box, one for FC and the other for processing the navigation sensor data; is there anything more to that navigation MCU?

PhucXDoan, 2025-10-06:
Tweaks to FBD:
- More information on the power distribution.
- Explicitly show 3 stepper motor drivers and have them be at 12V.
- Part number for LiPo batteries, which we used last year are from EEMB.

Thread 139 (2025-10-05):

RF Interfaces

lanaero, 2025-10-05:
Determine band and power of RF systems used by:

- [ ] CONSat
- [ ] Secondary Experiments

PhucXDoan, 2025-10-05:
@shelbyoVT, all I know for the ESPs is that they use 2.4GHz WiFI, but I'm not sure about power though, could you look into that?

@lanaero will you be looking into the secondary experiments yourself? I don't know much about Inspirefy's situation nor Denby's boards (@DRicevt).

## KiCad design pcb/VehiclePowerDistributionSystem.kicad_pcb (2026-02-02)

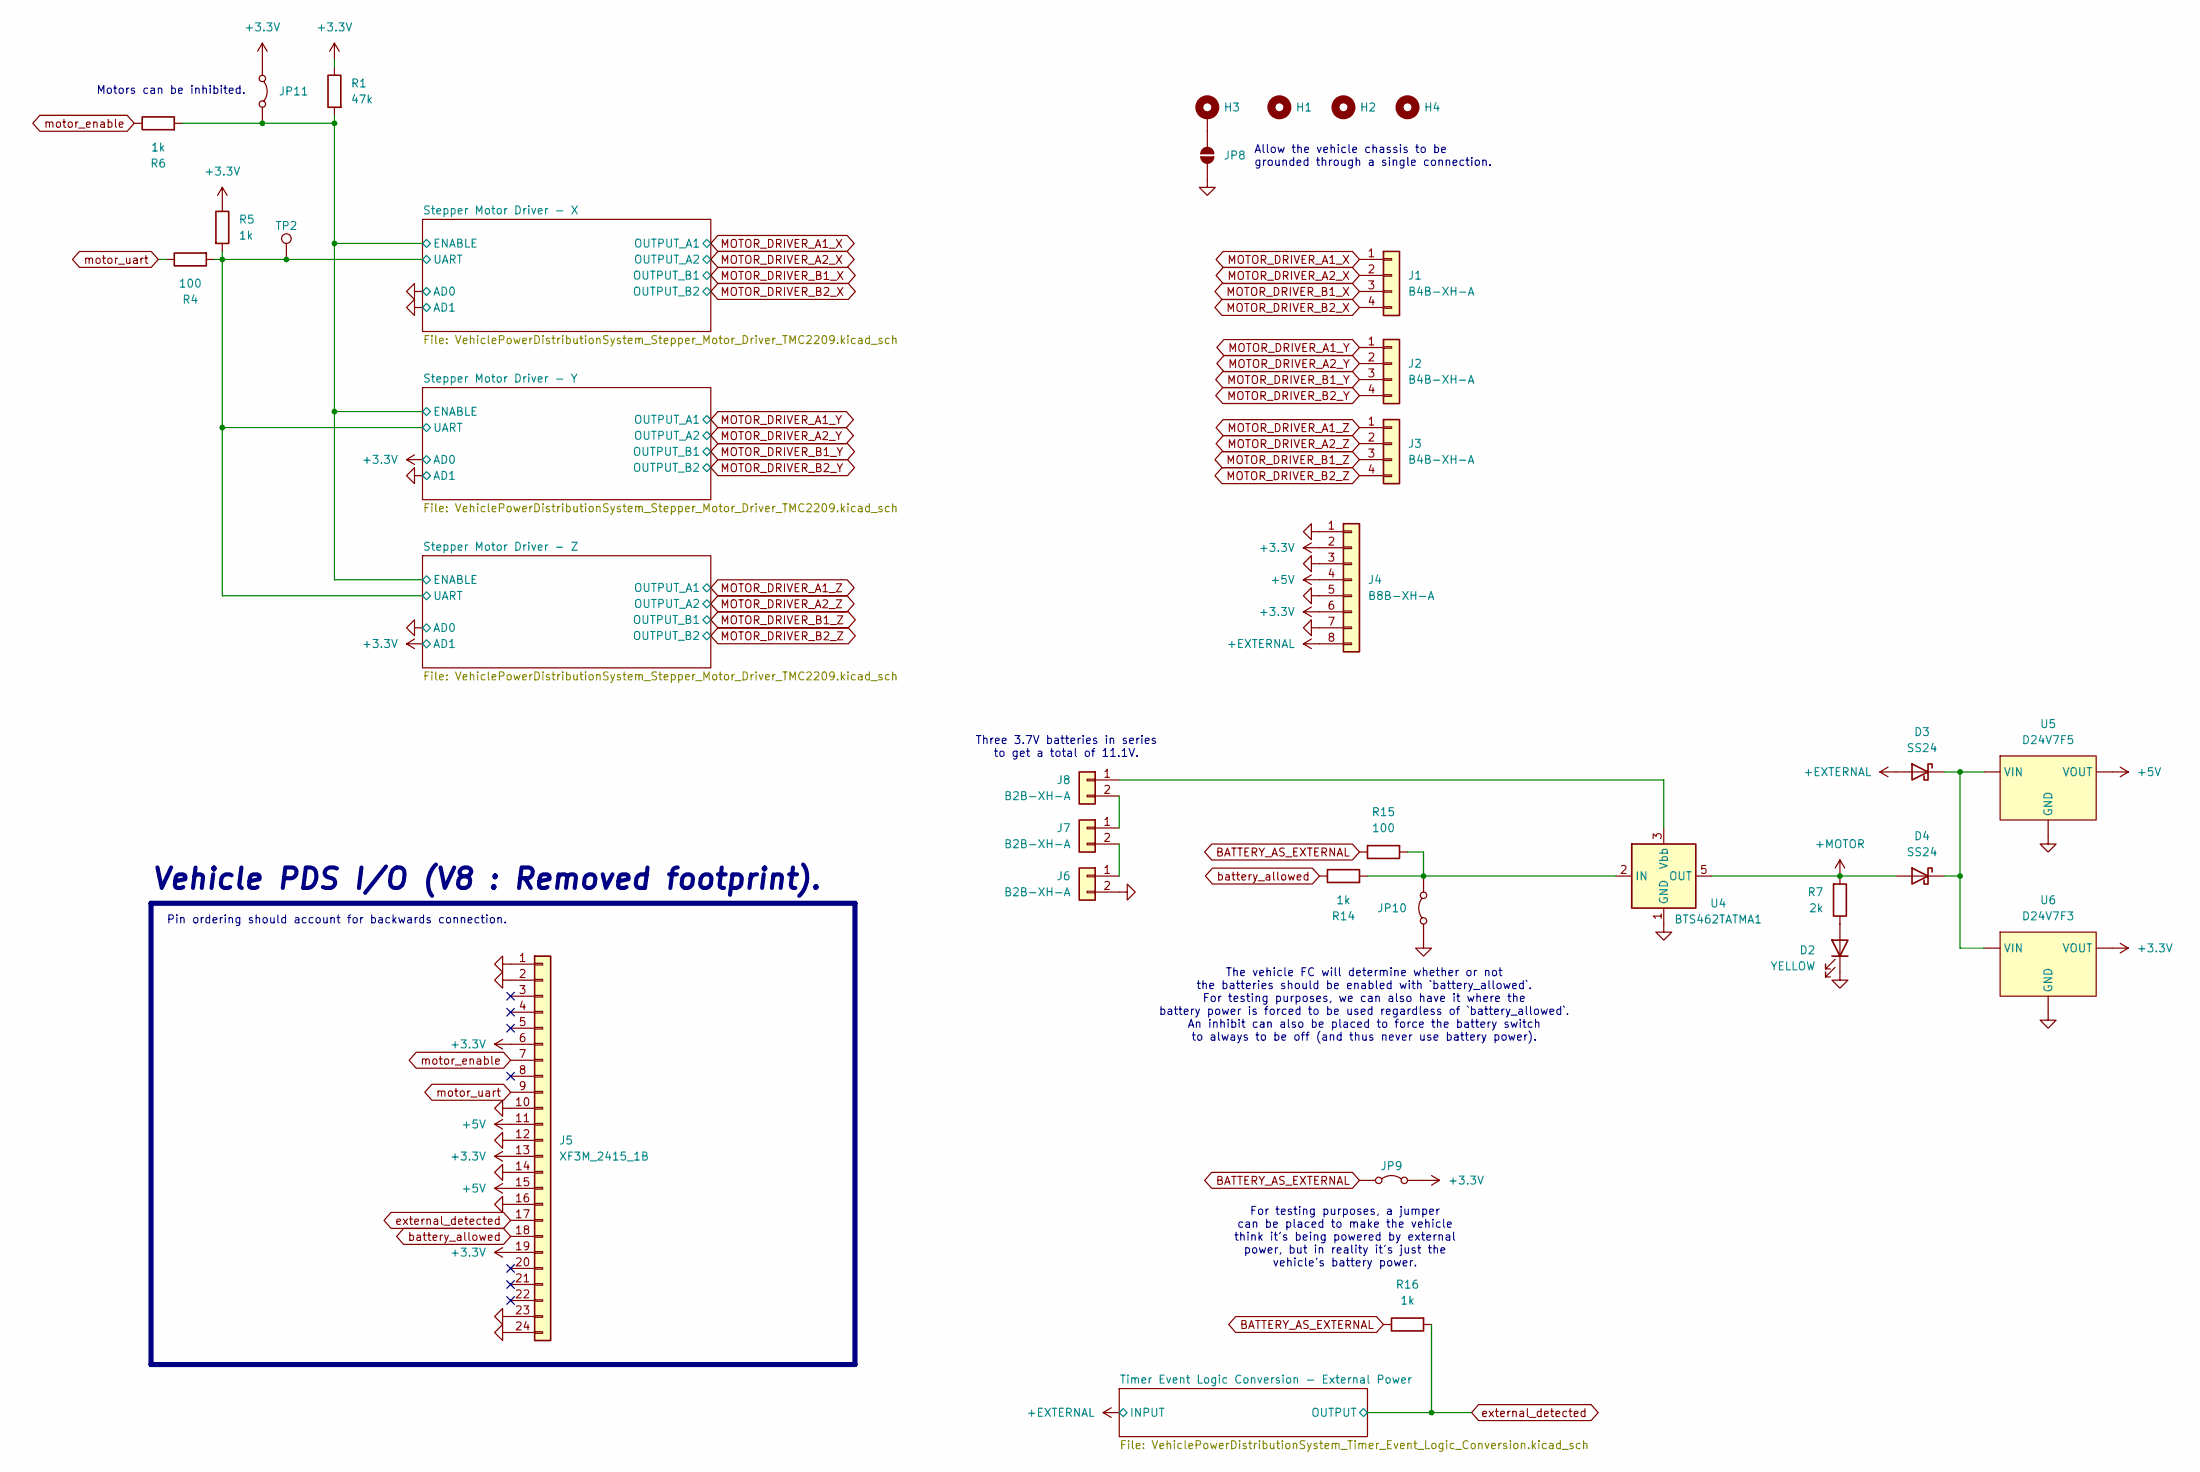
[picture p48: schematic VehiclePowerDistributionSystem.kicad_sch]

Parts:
D2: YELLOW; LED_1206_3216Metric_Pad1.42x1.75mm_HandSolder
D3, D4: SS24; D_SMA-SMB_Universal_Handsoldering
H1, H2, H4: MountingHole; MountingHole_3.2mm_M3
H3: MountingHole_Pad; MountingHole_3.2mm_M3_DIN965_Pad
J1, J2, J3: B4B-XH-A; JST_XH_B4B-XH-A_1x04_P2.50mm_Vertical
J4: B8B-XH-A; JST_XH_B8B-XH-A_1x08_P2.50mm_Vertical
J5: XF3M_2415_1B; XF3M_2415_1B - REVERSED
J6, J7, J8: B2B-XH-A; JST_XH_B2B-XH-A_1x02_P2.50mm_Vertical
JP8: SolderJumper_2_Open; SolderJumper-2_P1.3mm_Open_RoundedPad1.0x1.5mm
JP9, JP10, JP11: Jumper_2_Bridged; NPC02SXON-RC
R1: 47k; R_1206_3216Metric_Pad1.30x1.75mm_HandSolder
R4, R15: 100; R_1206_3216Metric_Pad1.30x1.75mm_HandSolder
R5, R6, R14, R16: 1k; R_1206_3216Metric_Pad1.30x1.75mm_HandSolder
R7: 2k; R_1206_3216Metric_Pad1.30x1.75mm_HandSolder
TP2: TestPoint; TestPoint_Bridge_Pitch2.0mm_Drill0.7mm
U4: BTS462TATMA1; TO-252-4
U5: D24V7F5; D24V7Fx
U6: D24V7F3; D24V7Fx

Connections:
+3.3V: J4.2, J4.6, J5.6, J5.13, J5.19, JP9.1 (A), JP11.1 (A), R1.1, R5.1, U6.VOUT; also elsewhere on the board
+5V: J4.4, J5.11, J5.15, U5.VOUT
+EXTERNAL: D3.2 (A), J4.8; also elsewhere on the board
+MOTOR: D4.2 (A), R7.2, U4.5 (OUT); also elsewhere on the board
/Stepper Motor Driver - X/ENABLE: JP11.2 (B), R1.2, R6.2; also elsewhere on the board
/Stepper Motor Driver - X/UART: R4.2, R5.2, TP2.1; also elsewhere on the board
BATTERY_AS_EXTERNAL: JP9.2 (B), R15.1, R16.1
GND: D2.1 (K), J4.1, J4.3, J4.5, J4.7, J5.1, J5.2, J5.10, J5.12, J5.14, J5.16, J5.23, J5.24, J6.2, JP8.1 (A), JP10.1 (A), U4.1 (GND), U5.GND, U6.GND; also elsewhere on the board
MOTOR_DRIVER_A1_X: J1.1; also elsewhere on the board
MOTOR_DRIVER_A1_Y: J2.1; also elsewhere on the board
MOTOR_DRIVER_A1_Z: J3.1; also elsewhere on the board
MOTOR_DRIVER_A2_X: J1.2; also elsewhere on the board
MOTOR_DRIVER_A2_Y: J2.2; also elsewhere on the board
MOTOR_DRIVER_A2_Z: J3.2; also elsewhere on the board
MOTOR_DRIVER_B1_X: J1.3; also elsewhere on the board
MOTOR_DRIVER_B1_Y: J2.3; also elsewhere on the board
MOTOR_DRIVER_B1_Z: J3.3; also elsewhere on the board
MOTOR_DRIVER_B2_X: J1.4; also elsewhere on the board
MOTOR_DRIVER_B2_Y: J2.4; also elsewhere on the board
MOTOR_DRIVER_B2_Z: J3.4; also elsewhere on the board
unnamed: D2.2 (A), R7.1
unnamed: D3.1 (K), D4.1 (K), U5.VIN, U6.VIN
unnamed: J6.1, J7.2
unnamed: J7.1, J8.2
unnamed: J8.1, U4.3 (Vbb)
unnamed: H3.1, JP8.2 (B)
unnamed: JP10.2 (B), R14.2, R15.2, U4.2 (IN)
battery_allowed: J5.18, R14.1
external_detected: J5.17, R16.2; also elsewhere on the board
motor_enable: J5.7, R6.1
motor_uart: J5.9, R4.1

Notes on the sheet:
Pin ordering should account for backwards connection.
Three 3.7V batteries in series to get a total of 11.1V.
Allow the vehicle chassis to be grounded through a single connection.
For testing purposes, a jumper can be placed to make the vehicle think it's being powered by external power, but in reality it's just the vehicle's battery power.
Vehicle PDS I/O (V8 : Removed footprint).
The vehicle FC will determine whether or not the batteries should be enabled with `battery_allowed`. For testing purposes, we can also have it where the battery power is forced to be used regardless of `battery_allowed`. An inhibit can also be placed to force the battery switch to always to be off 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
Motors can be inhibited.

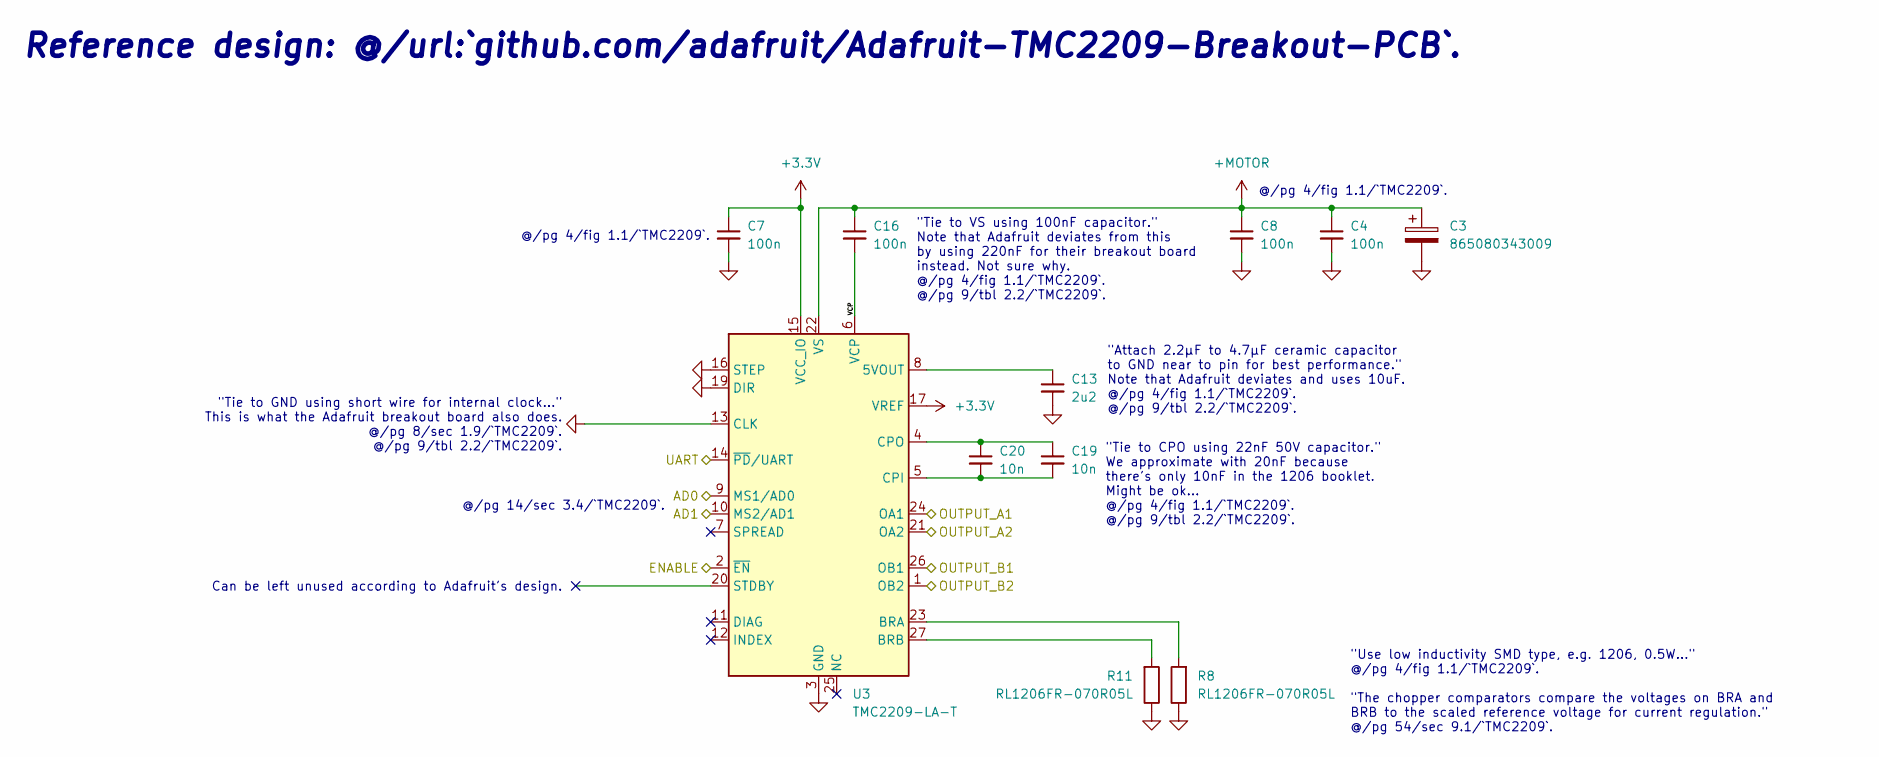
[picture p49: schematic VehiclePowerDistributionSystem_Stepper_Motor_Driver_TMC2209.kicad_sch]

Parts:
C3: 865080343009; CP_Elec_6.3x5.4
C4, C7, C8, C16: 100n; C_1206_3216Metric_Pad1.33x1.80mm_HandSolder
C13: 2u2; C_1206_3216Metric_Pad1.33x1.80mm_HandSolder
C19, C20: 10n; C_1206_3216Metric_Pad1.33x1.80mm_HandSolder
R8, R11: RL1206FR-070R05L; R_1206_3216Metric_Pad1.30x1.75mm_HandSolder
U3: TMC2209-LA-T; VQFN-28-1EP_5x5mm_P0.5mm_EP3.7x3.7mm_ThermalVias

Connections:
+3.3V: C7.1, U3.10 (MS2/AD1), U3.15 (VCC_IO), U3.17 (VREF); also elsewhere on the board
+MOTOR: C3.1, C4.1, C8.1, C16.1, U3.22 (VS), U3.28 (VS); also elsewhere on the board
/Stepper Motor Driver - X/ENABLE: U3.2 (~EN); also elsewhere on the board
/Stepper Motor Driver - X/UART: U3.14 (~PD/UART); also elsewhere on the board
/Stepper Motor Driver - Z/VCP: C16.2, U3.6 (VCP)
GND: C3.2, C4.2, C7.2, C8.2, C13.2, R8.1, R11.1, U3.3 (GND), U3.9 (MS1/AD0), U3.13 (CLK), U3.16 (STEP), U3.18 (GND), U3.19 (DIR), U3.29 (GND); also elsewhere on the board
MOTOR_DRIVER_A1_Z: U3.24 (OA1); also elsewhere on the board
MOTOR_DRIVER_A2_Z: U3.21 (OA2); also elsewhere on the board
MOTOR_DRIVER_B1_Z: U3.26 (OB1); also elsewhere on the board
MOTOR_DRIVER_B2_Z: U3.1 (OB2); also elsewhere on the board
unnamed: C13.1, U3.8 (5VOUT)
unnamed: R8.2, U3.23 (BRA)
unnamed: R11.2, U3.27 (BRB)
unnamed: C19.2, C20.2, U3.5 (CPI)
unnamed: C19.1, C20.1, U3.4 (CPO)

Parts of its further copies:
C1, C2: 865080343009; CP_Elec_6.3x5.4
C5, C6, C9, C10, C11, C12, C17, C18: 100n; C_1206_3216Metric_Pad1.33x1.80mm_HandSolder
C14, C15: 2u2; C_1206_3216Metric_Pad1.33x1.80mm_HandSolder
C21, C22, C23, C24: 10n; C_1206_3216Metric_Pad1.33x1.80mm_HandSolder
R9, R10, R12, R13: RL1206FR-070R05L; R_1206_3216Metric_Pad1.30x1.75mm_HandSolder
U1, U2: TMC2209-LA-T; VQFN-28-1EP_5x5mm_P0.5mm_EP3.7x3.7mm_ThermalVias

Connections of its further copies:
+3.3V: C9.1, C11.1, U1.15 (VCC_IO), U1.17 (VREF), U2.9 (MS1/AD0), U2.15 (VCC_IO), U2.17 (VREF); also elsewhere on the board
+MOTOR: C1.1, C2.1, C5.1, C6.1, C10.1, C12.1, C17.1, C18.1, U1.22 (VS), U1.28 (VS), U2.22 (VS), U2.28 (VS); also elsewhere on the board
/Stepper Motor Driver - X/ENABLE: U1.2 (~EN), U2.2 (~EN); also elsewhere on the board
/Stepper Motor Driver - X/UART: U1.14 (~PD/UART), U2.14 (~PD/UART); also elsewhere on the board
/Stepper Motor Driver - X/VCP: C18.2, U1.6 (VCP)
/Stepper Motor Driver - Y/VCP: C17.2, U2.6 (VCP)
GND: C1.2, C2.2, C5.2, C6.2, C9.2, C10.2, C11.2, C12.2, C14.2, C15.2, R9.1, R10.1, R12.1, R13.1, U1.3 (GND), U1.9 (MS1/AD0), U1.10 (MS2/AD1), U1.13 (CLK), U1.16 (STEP), U1.18 (GND), U1.19 (DIR), U1.29 (GND), U2.3 (GND), U2.10 (MS2/AD1), U2.13 (CLK), U2.16 (STEP), U2.18 (GND), U2.19 (DIR), U2.29 (GND); also elsewhere on the board
MOTOR_DRIVER_A1_X: U1.24 (OA1); also elsewhere on the board
MOTOR_DRIVER_A1_Y: U2.24 (OA1); also elsewhere on the board
MOTOR_DRIVER_A2_X: U1.21 (OA2); also elsewhere on the board
MOTOR_DRIVER_A2_Y: U2.21 (OA2); also elsewhere on the board
MOTOR_DRIVER_B1_X: U1.26 (OB1); also elsewhere on the board
MOTOR_DRIVER_B1_Y: U2.26 (OB1); also elsewhere on the board
MOTOR_DRIVER_B2_X: U1.1 (OB2); also elsewhere on the board
MOTOR_DRIVER_B2_Y: U2.1 (OB2); also elsewhere on the board
unnamed: C15.1, U1.8 (5VOUT)
unnamed: R10.2, U1.23 (BRA)
unnamed: R13.2, U1.27 (BRB)
unnamed: C23.2, C24.2, U1.5 (CPI)
unnamed: C23.1, C24.1, U1.4 (CPO)
unnamed: C14.1, U2.8 (5VOUT)
unnamed: R9.2, U2.23 (BRA)
unnamed: R12.2, U2.27 (BRB)
unnamed: C21.2, C22.2, U2.5 (CPI)
unnamed: C21.1, C22.1, U2.4 (CPO)

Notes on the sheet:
"Tie to CPO using 22nF 50V capacitor." We approximate with 20nF because there's only 10nF in the 1206 booklet. Might be ok... @/pg 4/fig 1.1/`TMC2209`. @/pg 9/tbl 2.2/`TMC2209`.
Reference design: @/url:`github.com/adafruit/Adafruit-TMC2209-Breakout-PCB`.
@/pg 4/fig 1.1/`TMC2209`.
Can be left unused according to Adafruit's design.
@/pg 14/sec 3.4/`TMC2209`.
"Tie to GND using short wire for internal clock..." This is what the Adafruit breakout board also does. @/pg 8/sec 1.9/`TMC2209`. @/pg 9/tbl 2.2/`TMC2209`.
"Use low inductivity SMD type, e.g. 1206, 0.5W..." @/pg 4/fig 1.1/`TMC2209`. "The chopper comparators compare the voltages on BRA and BRB to the scaled reference voltage for current regulation." @/pg 54/sec 9.1/`TMC2209`.
"Tie to VS using 100nF capacitor." Note that Adafruit deviates from this by using 220nF for their breakout board instead. Not sure why. @/pg 4/fig 1.1/`TMC2209`. @/pg 9/tbl 2.2/`TMC2209`.
"Attach 2.2μF to 4.7μF ceramic capacitor to GND near to pin for best performance." Note that Adafruit deviates and uses 10uF. @/pg 4/fig 1.1/`TMC2209`. @/pg 9/tbl 2.2/`TMC2209`.

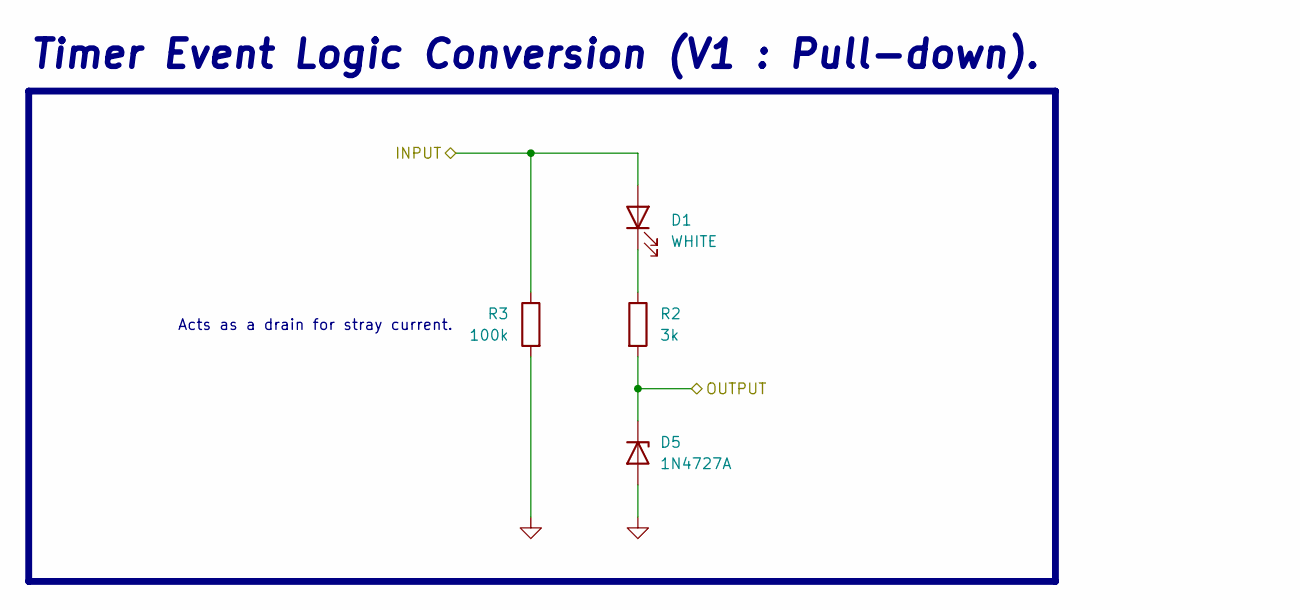
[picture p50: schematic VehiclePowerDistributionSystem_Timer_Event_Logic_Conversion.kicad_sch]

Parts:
D1: WHITE; LED_1206_3216Metric_Pad1.42x1.75mm_HandSolder
D5: 1N4727A; D_A-405_P7.62mm_Horizontal
R2: 3k; R_1206_3216Metric_Pad1.30x1.75mm_HandSolder
R3: 100k; R_1206_3216Metric_Pad1.30x1.75mm_HandSolder

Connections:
+EXTERNAL: D1.2 (A), R3.1; also elsewhere on the board
GND: D5.2 (A), R3.2; also elsewhere on the board
unnamed: D1.1 (K), R2.1
external_detected: D5.1 (K), R2.2; also elsewhere on the board

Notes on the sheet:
Timer Event Logic Conversion (V1 : Pull-down).
Acts as a drain for stray current.

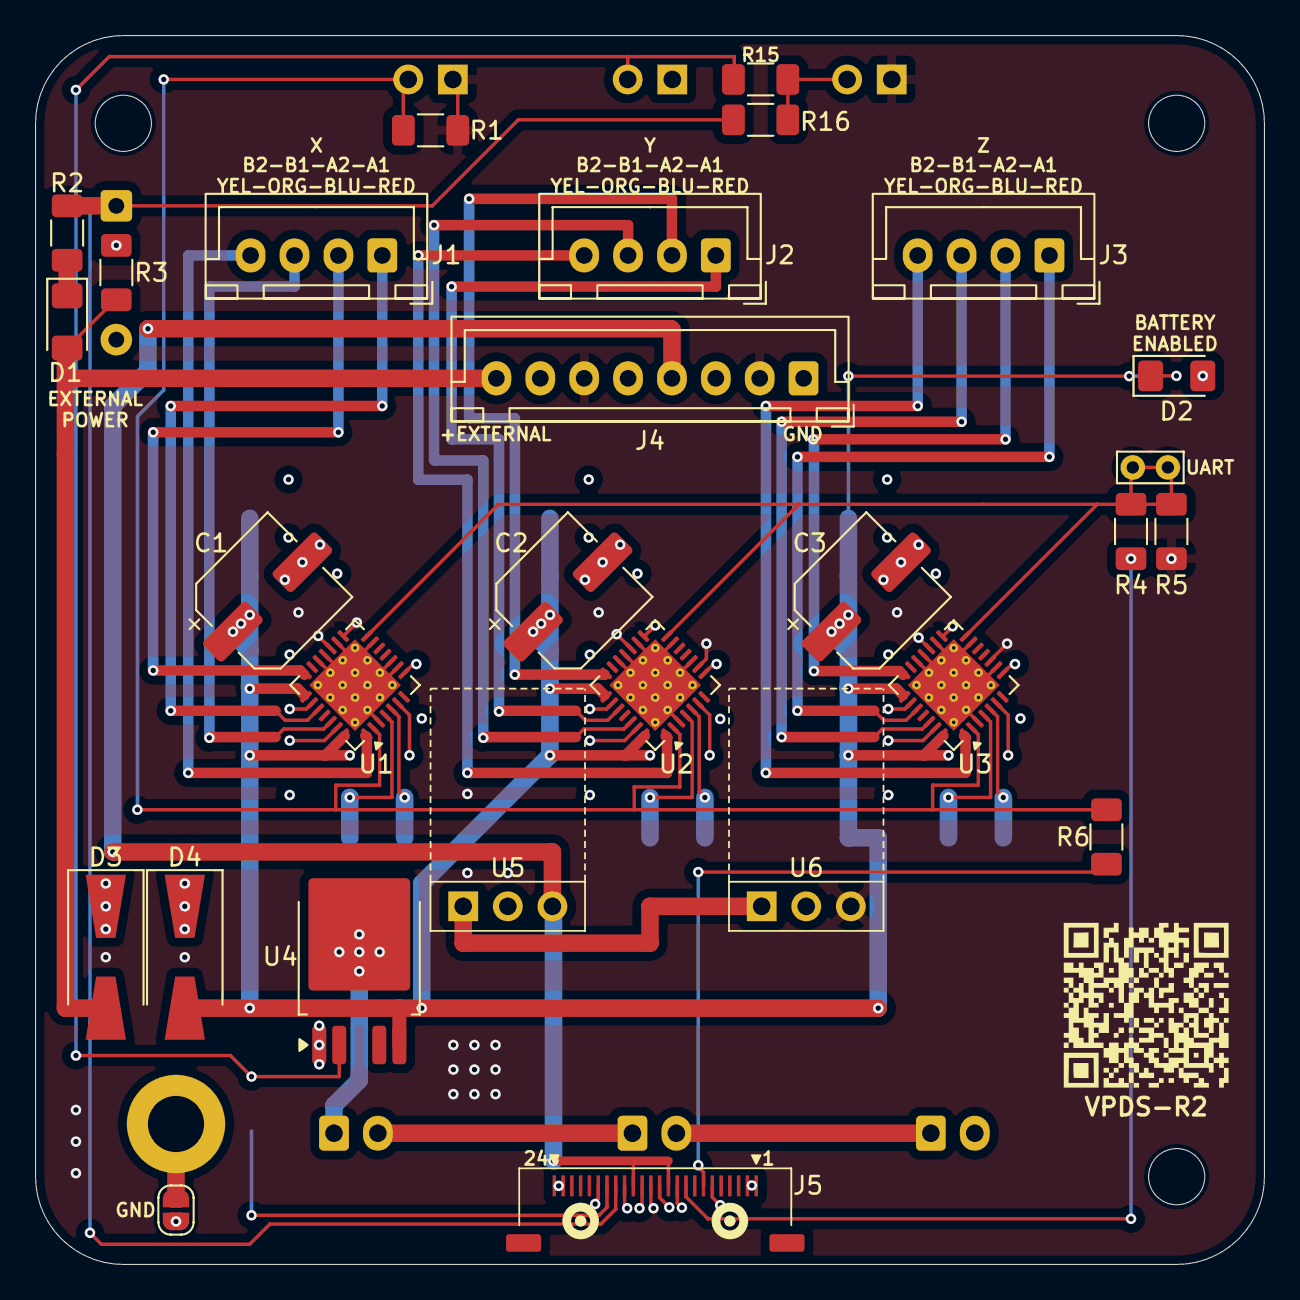
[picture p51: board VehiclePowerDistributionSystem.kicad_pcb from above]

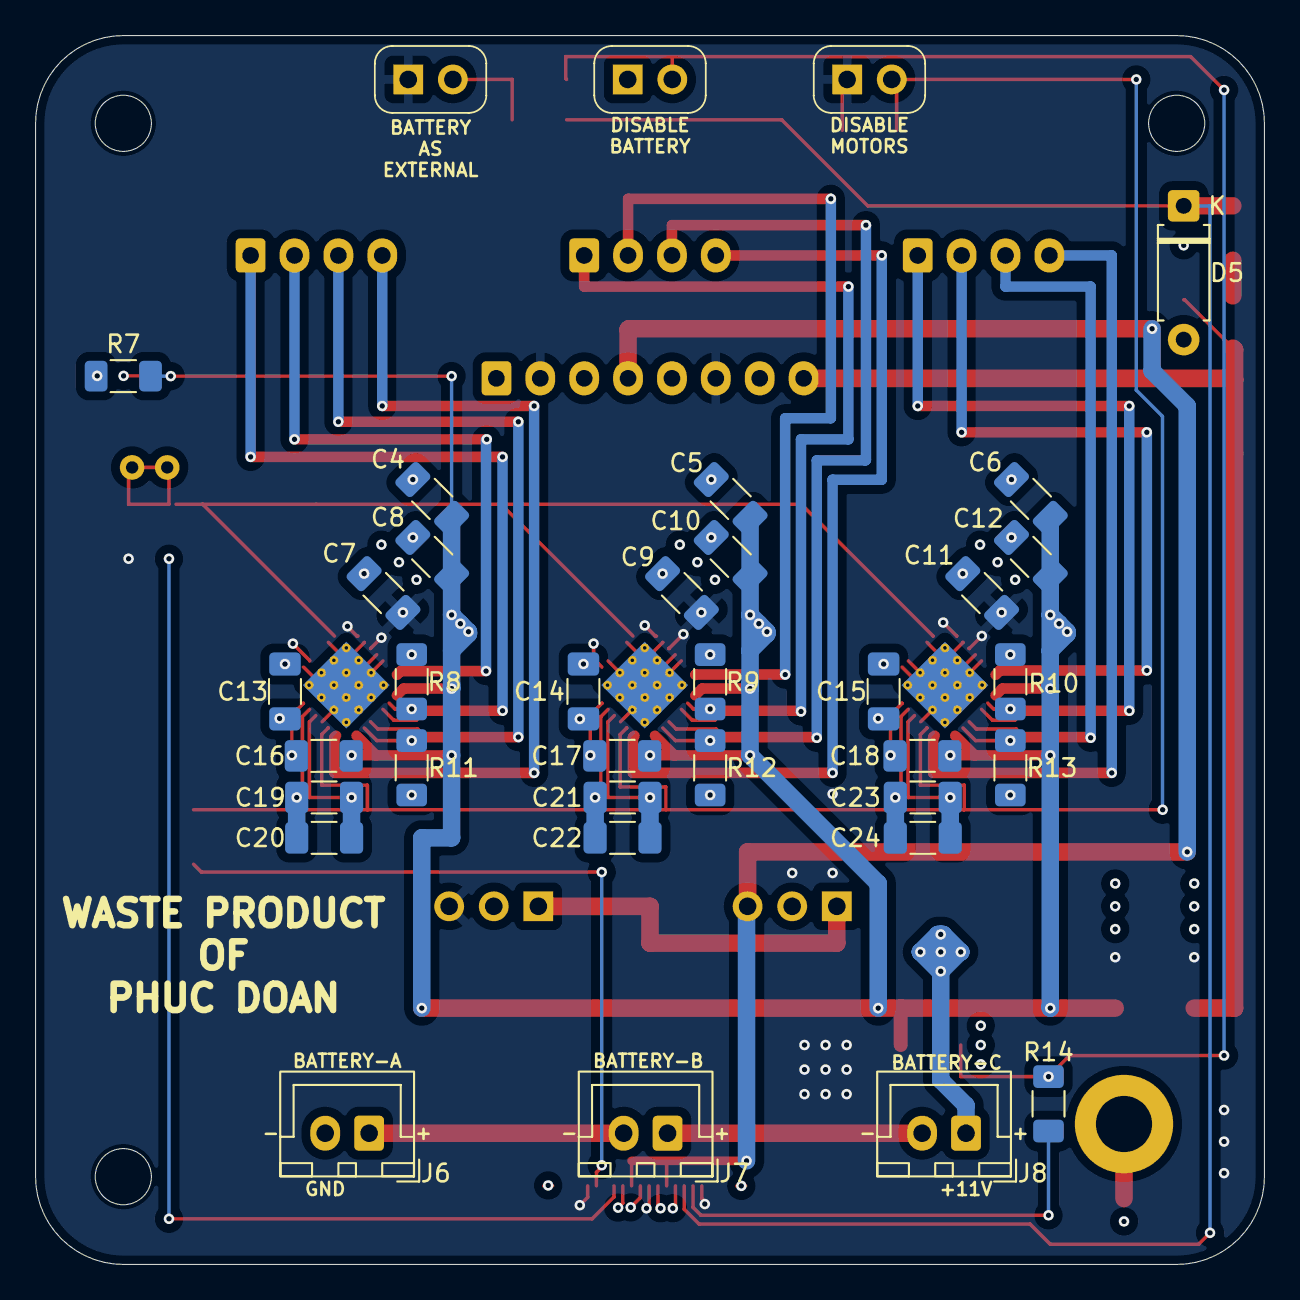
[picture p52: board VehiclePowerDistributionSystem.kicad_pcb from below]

Board: 4 copper layers, 70.0 x 70.0 mm, 69 parts (36 on the bottom side), 50 nets.

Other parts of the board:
N1: Housing; Dummy

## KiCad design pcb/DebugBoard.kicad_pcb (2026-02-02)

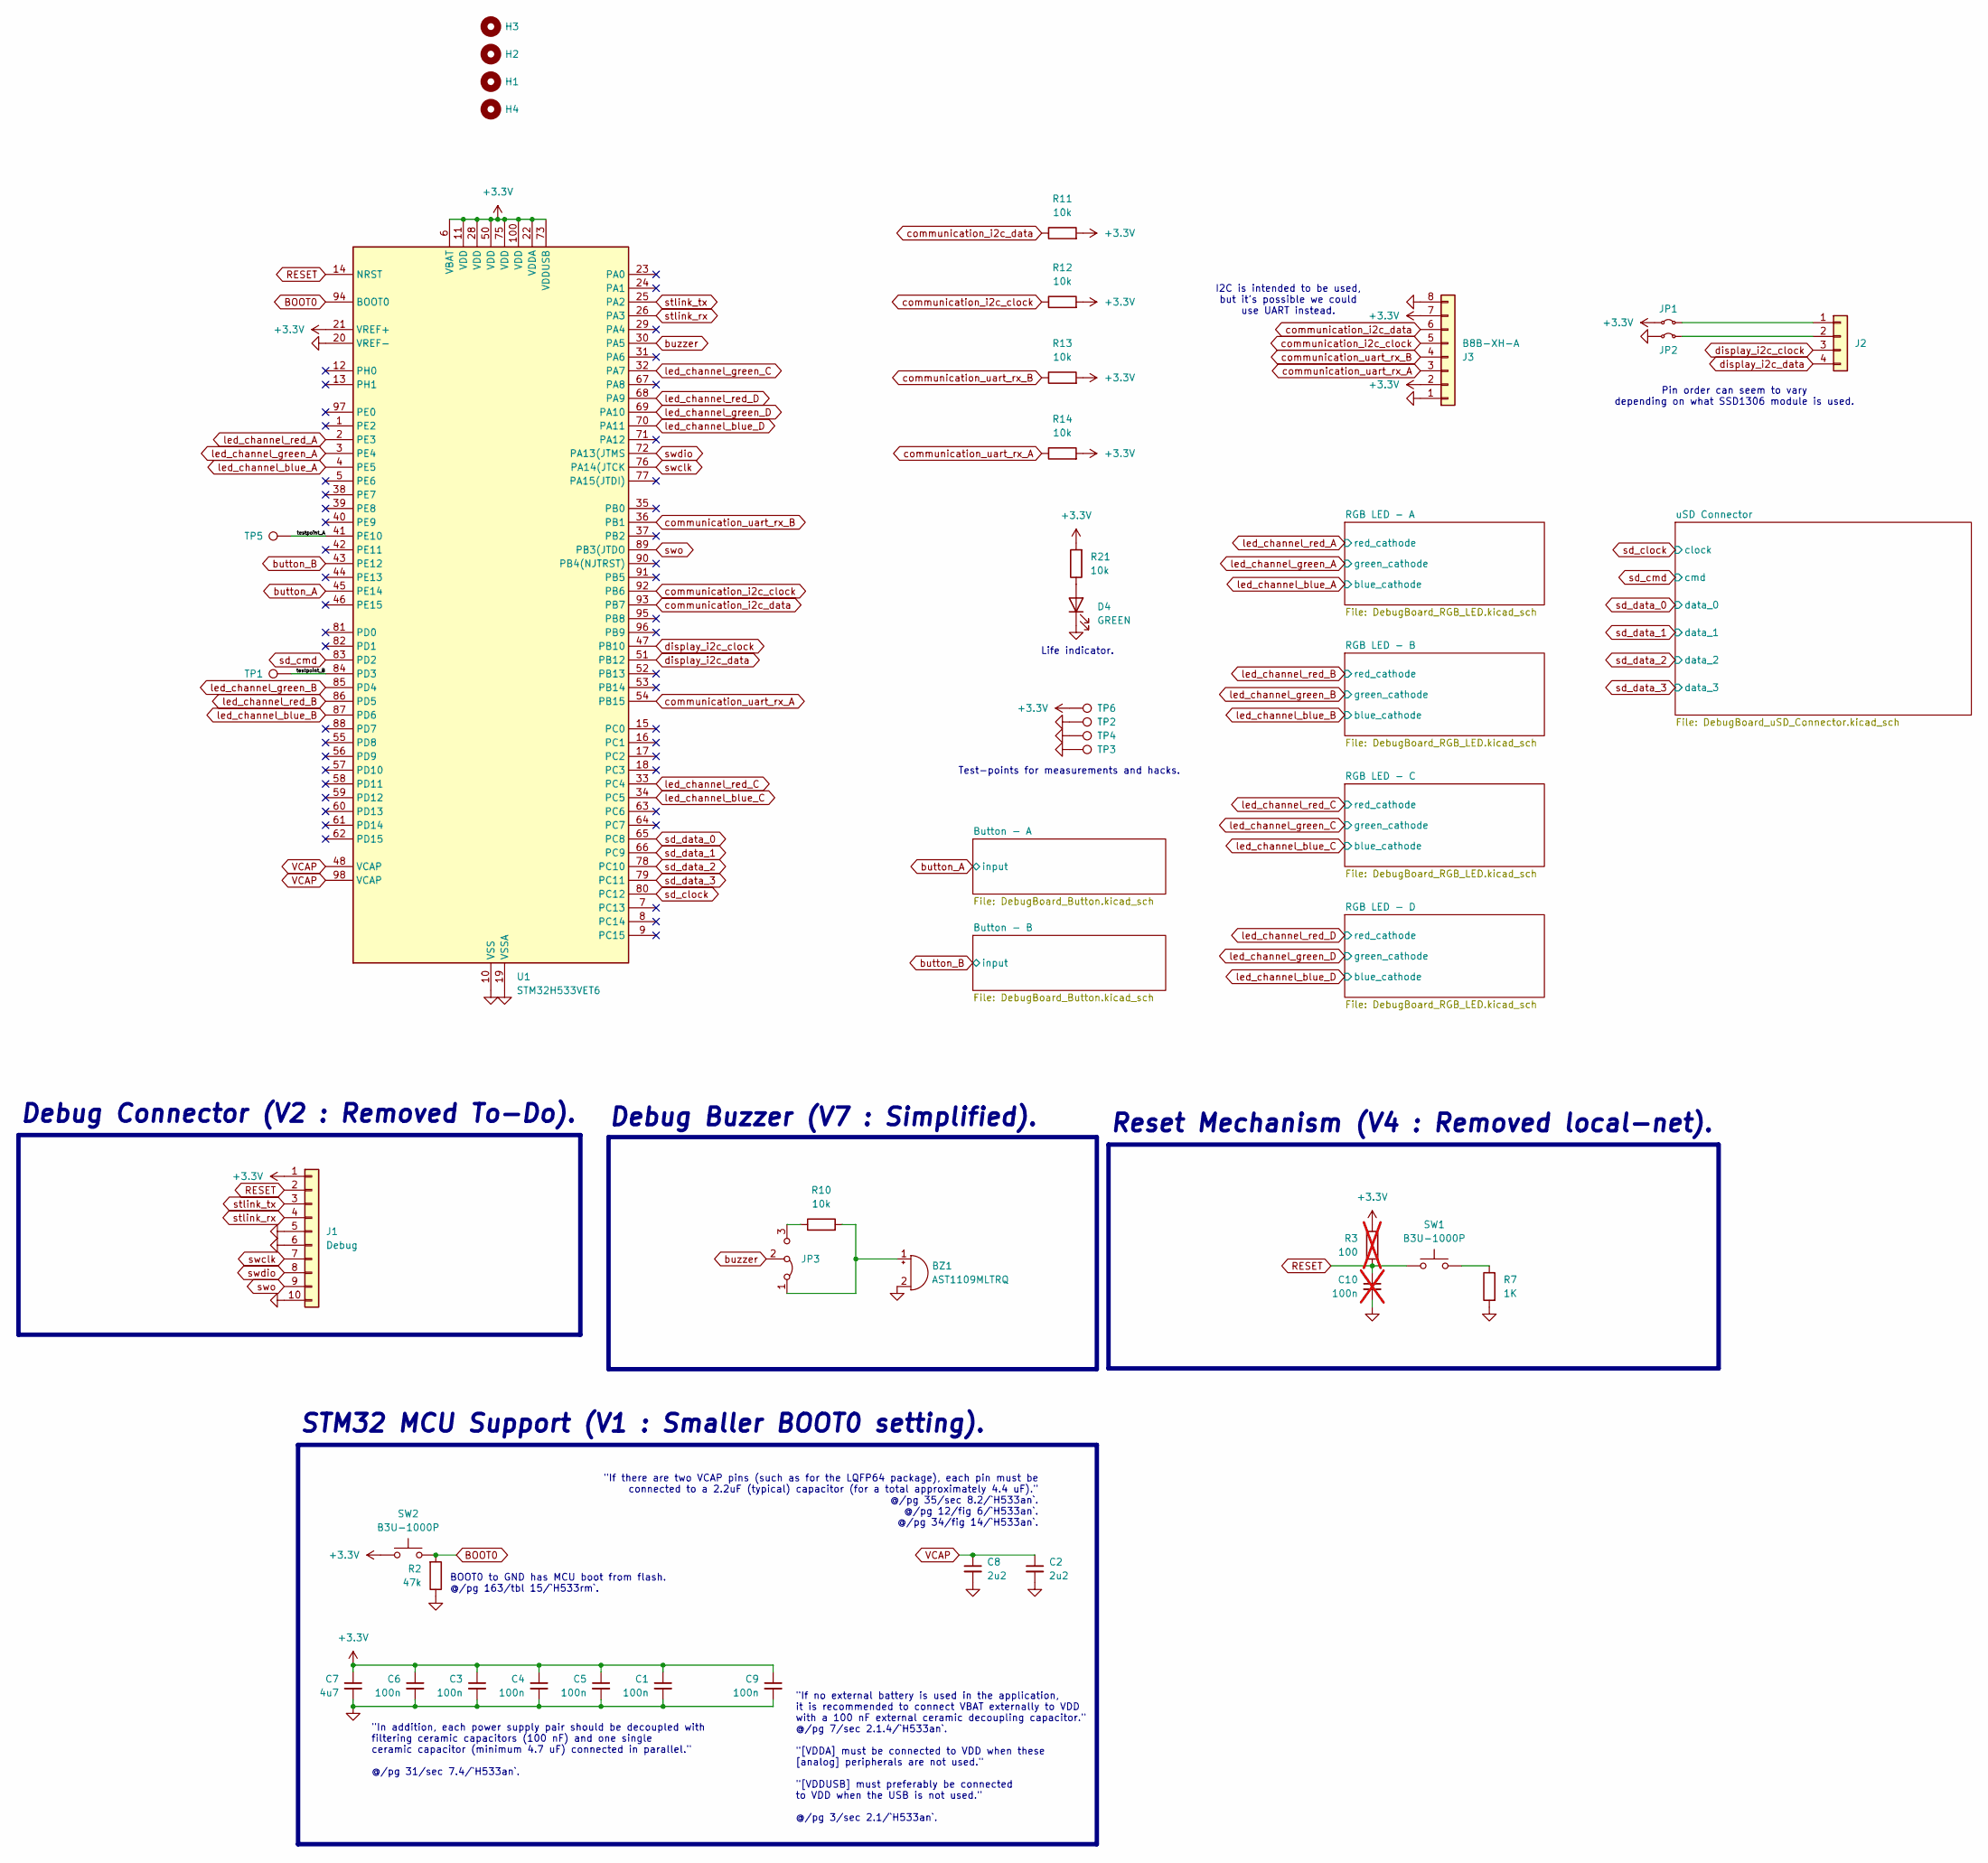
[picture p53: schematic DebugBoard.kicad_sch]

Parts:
BZ1: AST1109MLTRQ; Buzzer_Mallory_AST1109MLTRQ
C1, C3, C4, C5, C6, C9: 100n; C_1206_3216Metric_Pad1.33x1.80mm_HandSolder
C2, C8: 2u2; C_1206_3216Metric_Pad1.33x1.80mm_HandSolder
C7: 4u7; C_1206_3216Metric_Pad1.33x1.80mm_HandSolder
C10: 100n; C_1206_3216Metric_Pad1.33x1.80mm_HandSolder; not fitted
D4: GREEN; LED_1206_3216Metric_Pad1.42x1.75mm_HandSolder
H1, H2, H3, H4: MountingHole; MountingHole_3.2mm_M3
J1: Debug; Molex_PicoBlade_53047-1010_1x10_P1.25mm_Vertical
J2: Conn_01x04; SSD1306_Module_Connector
J3: B8B-XH-A; JST_XH_B8B-XH-A_1x08_P2.50mm_Vertical
JP1, JP2: Jumper_2_Small_Bridged; TestPoint_2Pads_Pitch2.54mm_Drill0.8mm
JP3: Jumper_3_Bridged12; PinHeader_1x03_P2.54mm_Vertical
R2: 47k; R_1206_3216Metric_Pad1.30x1.75mm_HandSolder
R3: 100; R_1206_3216Metric_Pad1.30x1.75mm_HandSolder; not fitted
R7: 1K; R_1206_3216Metric_Pad1.30x1.75mm_HandSolder
R10, R11, R12, R13, R14, R21: 10k; R_1206_3216Metric_Pad1.30x1.75mm_HandSolder
SW1, SW2: B3U-1000P; SW_SPST_B3U-1000P
TP1, TP2, TP3, TP4, TP5, TP6: TestPoint; TestPoint_Bridge_Pitch2.0mm_Drill0.7mm
U1: STM32H533VET6; LQFP-100_14x14mm_P0.5mm

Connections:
+3.3V: C1.1, C3.1, C4.1, C5.1, C6.1, C7.1, C9.1, J1.1, J3.2, J3.7, JP1.1 (A), R3.1, R11.2, R12.2, R13.2, R14.2, R21.2, SW2.1, TP6.1, U1.6 (VBAT), U1.11 (VDD), U1.21 (VREF+), U1.22 (VDDA), U1.28 (VDD), U1.50 (VDD), U1.73 (VDDUSB), U1.75 (VDD), U1.100 (VDD); also elsewhere on the board
/testpoint_A: TP5.1, U1.41 (PE10)
/testpoint_B: TP1.1, U1.84 (PD3)
BOOT0: R2.2, SW2.2, U1.94 (BOOT0)
GND: BZ1.2 (-), C1.2, C2.2, C3.2, C4.2, C5.2, C6.2, C7.2, C8.2, C9.2, C10.2, D4.1 (K), J1.5, J1.6, J1.10, J3.1, J3.8, JP2.1 (A), R2.1, R7.2, TP2.1, TP3.1, TP4.1, U1.10 (VSS), U1.19 (VSSA), U1.20 (VREF-), U1.27 (VSS), U1.49 (VSS), U1.74 (VSS), U1.99 (VSS); also elsewhere on the board
unnamed: BZ1.1 (+), JP3.1 (A), R10.2
unnamed: D4.2 (A), R21.1
unnamed: J2.1, JP1.2 (B)
unnamed: J2.2, JP2.2 (B)
unnamed: JP3.3 (B), R10.1
unnamed: R7.1, SW1.2
RESET: C10.1, J1.2, R3.2, SW1.1, U1.14 (NRST)
VCAP: C2.1, C8.1, U1.48 (VCAP), U1.98 (VCAP)
button_A: U1.45 (PE14); also elsewhere on the board
button_B: U1.43 (PE12); also elsewhere on the board
buzzer: JP3.2 (C), U1.30 (PA5)
communication_i2c_clock: J3.5, R12.1, U1.92 (PB6)
communication_i2c_data: J3.6, R11.1, U1.93 (PB7)
communication_uart_rx_A: J3.3, R14.1, U1.54 (PB15)
communication_uart_rx_B: J3.4, R13.1, U1.36 (PB1)
display_i2c_clock: J2.3, U1.47 (PB10)
display_i2c_data: J2.4, U1.51 (PB12)
led_channel_blue_A: U1.4 (PE5); also elsewhere on the board
led_channel_blue_B: U1.87 (PD6); also elsewhere on the board
led_channel_blue_C: U1.34 (PC5); also elsewhere on the board
led_channel_blue_D: U1.70 (PA11); also elsewhere on the board
led_channel_green_A: U1.3 (PE4); also elsewhere on the board
led_channel_green_B: U1.85 (PD4); also elsewhere on the board
led_channel_green_C: U1.32 (PA7); also elsewhere on the board
led_channel_green_D: U1.69 (PA10); also elsewhere on the board
led_channel_red_A: U1.2 (PE3); also elsewhere on the board
led_channel_red_B: U1.86 (PD5); also elsewhere on the board
led_channel_red_C: U1.33 (PC4); also elsewhere on the board
led_channel_red_D: U1.68 (PA9); also elsewhere on the board
sd_clock: U1.80 (PC12); also elsewhere on the board
sd_cmd: U1.83 (PD2); also elsewhere on the board
sd_data_0: U1.65 (PC8); also elsewhere on the board
sd_data_1: U1.66 (PC9); also elsewhere on the board
sd_data_2: U1.78 (PC10); also elsewhere on the board
sd_data_3: U1.79 (PC11); also elsewhere on the board
stlink_rx: J1.4, U1.26 (PA3)
stlink_tx: J1.3, U1.25 (PA2)
swclk: J1.7, U1.76 (PA14(JTCK)
swdio: J1.8, U1.72 (PA13(JTMS)
swo: J1.9, U1.89 (PB3(JTDO)

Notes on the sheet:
STM32 MCU Support (V1 : Smaller BOOT0 setting).
Pin order can seem to vary depending on what SSD1306 module is used.
I2C is intended to be used, but it's possible we could use UART instead.
Reset Mechanism (V4 : Removed local-net).
Debug Connector (V2 : Removed To-Do).
BOOT0 to GND has MCU boot from flash. @/pg 163/tbl 15/`H533rm`.
Life indicator.
Test-points for measurements and hacks.
"If there are two VCAP pins (such as for the LQFP64 package), each pin must be connected to a 2.2uF (typical) capacitor (for a total approximately 4.4 uF)." @/pg 35/sec 8.2/`H533an`. @/pg 12/fig 6/`H533an`. @/pg 34/fig 14/`H533an`.
"In addition, each power supply pair should be decoupled with filtering ceramic capacitors (100 nF) and one single ceramic capacitor (minimum 4.7 uF) connected in parallel." @/pg 31/sec 7.4/`H533an`.
"If no external battery is used in the application, it is recommended to connect VBAT externally to VDD with a 100 nF external ceramic decoupling capacitor." @/pg 7/sec 2.1.4/`H533an`. "[VDDA] must be connected to VDD when these [analog] peripherals are not used." "[VDDUSB] must preferably be conne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
Debug Buzzer (V7 : Simplified).

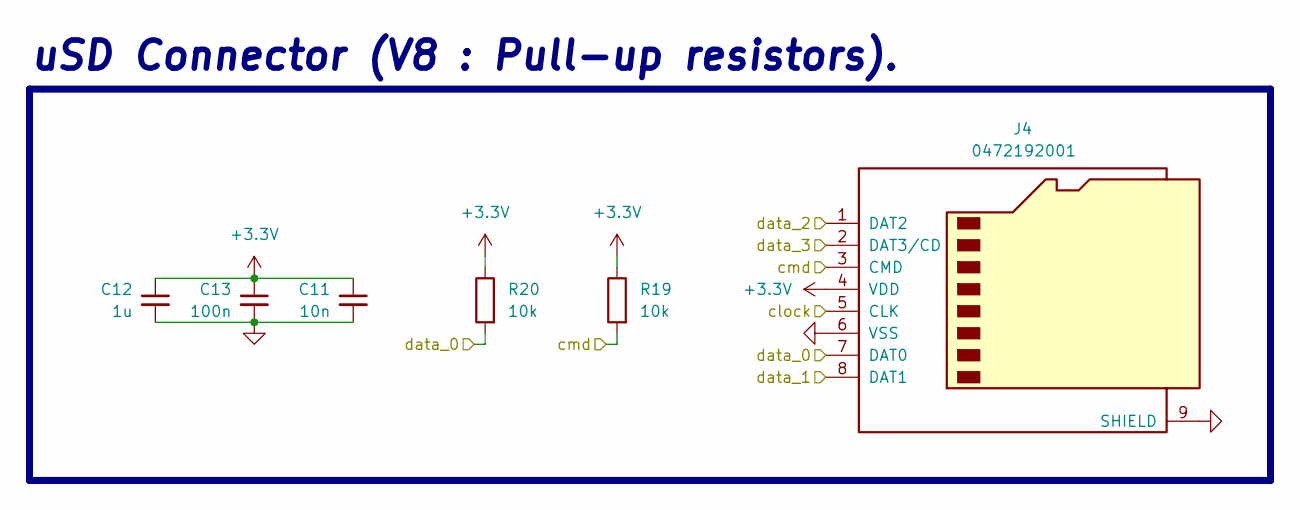
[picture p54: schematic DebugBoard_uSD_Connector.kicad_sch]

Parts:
C11: 10n; C_1206_3216Metric_Pad1.33x1.80mm_HandSolder
C12: 1u; C_1206_3216Metric_Pad1.33x1.80mm_HandSolder
C13: 100n; C_1206_3216Metric_Pad1.33x1.80mm_HandSolder
J4: 0472192001; microSD_HC_Molex_47219-2001
R19, R20: 10k; R_1206_3216Metric_Pad1.30x1.75mm_HandSolder

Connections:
+3.3V: C11.1, C12.1, C13.1, J4.4 (VDD), R19.1, R20.1; also elsewhere on the board
GND: C11.2, C12.2, C13.2, J4.6 (VSS), J4.9 (SHIELD); also elsewhere on the board
sd_clock: J4.5 (CLK); also elsewhere on the board
sd_cmd: J4.3 (CMD), R19.2; also elsewhere on the board
sd_data_0: J4.7 (DAT0), R20.2; also elsewhere on the board
sd_data_1: J4.8 (DAT1); also elsewhere on the board
sd_data_2: J4.1 (DAT2); also elsewhere on the board
sd_data_3: J4.2 (DAT3/CD); also elsewhere on the board

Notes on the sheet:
uSD Connector (V8 : Pull-up resistors).

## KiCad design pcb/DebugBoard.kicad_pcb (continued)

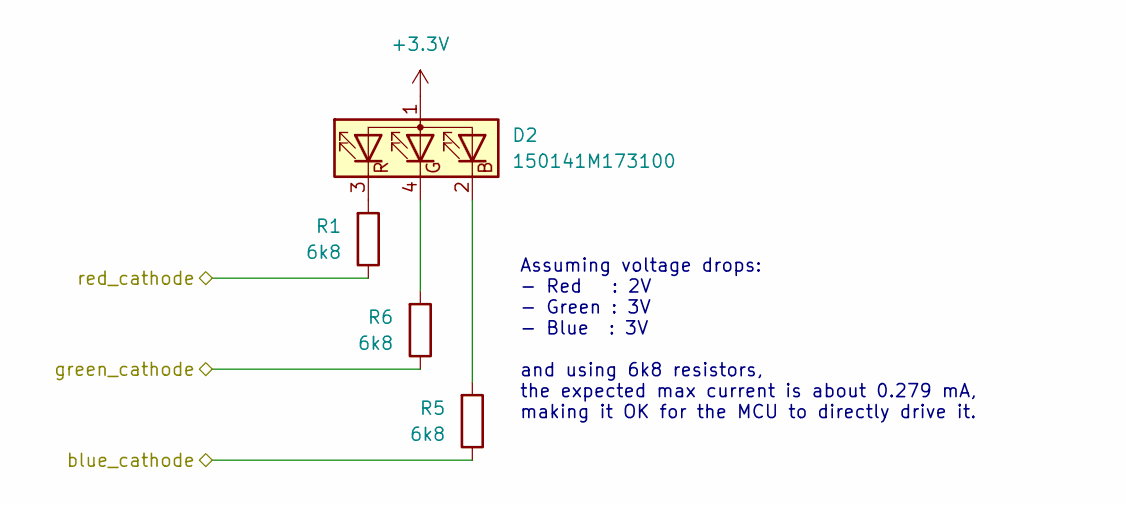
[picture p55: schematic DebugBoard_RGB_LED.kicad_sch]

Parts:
D2: 150141M173100; LED_RGB_Wuerth-PLCC4_3.2x2.8mm_150141M173100
R1, R5, R6: 6k8; R_1206_3216Metric_Pad1.30x1.75mm_HandSolder

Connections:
+3.3V: D2.1 (A); also elsewhere on the board
unnamed: D2.2 (BK), R5.2
unnamed: D2.4 (GK), R6.2
unnamed: D2.3 (RK), R1.2
led_channel_blue_A: R5.1; also elsewhere on the board
led_channel_green_A: R6.1; also elsewhere on the board
led_channel_red_A: R1.1; also elsewhere on the board

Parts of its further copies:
D1, D3, D5: 150141M173100; LED_RGB_Wuerth-PLCC4_3.2x2.8mm_150141M173100
R4, R8, R9, R17, R18, R22, R23, R24, R25: 6k8; R_1206_3216Metric_Pad1.30x1.75mm_HandSolder

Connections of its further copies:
+3.3V: D1.1 (A), D3.1 (A), D5.1 (A); also elsewhere on the board
unnamed: D1.2 (BK), R8.2
unnamed: D1.4 (GK), R9.2
unnamed: D1.3 (RK), R4.2
unnamed: D3.2 (BK), R22.2
unnamed: D3.4 (GK), R23.2
unnamed: D3.3 (RK), R25.2
unnamed: D5.2 (BK), R18.2
unnamed: D5.4 (GK), R17.2
unnamed: D5.3 (RK), R24.2
led_channel_blue_B: R8.1; also elsewhere on the board
led_channel_blue_C: R18.1; also elsewhere on the board
led_channel_blue_D: R22.1; also elsewhere on the board
led_channel_green_B: R9.1; also elsewhere on the board
led_channel_green_C: R17.1; also elsewhere on the board
led_channel_green_D: R23.1; also elsewhere on the board
led_channel_red_B: R4.1; also elsewhere on the board
led_channel_red_C: R24.1; also elsewhere on the board
led_channel_red_D: R25.1; also elsewhere on the board

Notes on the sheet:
Assuming voltage drops: - Red : 2V - Green : 3V - Blue : 3V and using 6k8 resistors, the expected max current is about 0.279 mA, making it OK for the MCU to directly drive it.

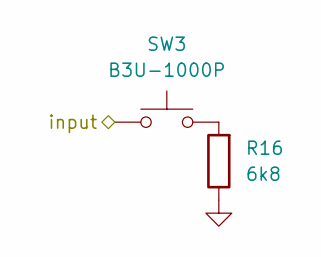
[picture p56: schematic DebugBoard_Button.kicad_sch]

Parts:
R16: 6k8; R_1206_3216Metric_Pad1.30x1.75mm_HandSolder
SW3: B3U-1000P; SW_SPST_B3U-1000P

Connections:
GND: R16.1; also elsewhere on the board
unnamed: R16.2, SW3.2
button_A: SW3.1; also elsewhere on the board

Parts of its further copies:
R15: 6k8; R_1206_3216Metric_Pad1.30x1.75mm_HandSolder
SW4: B3U-1000P; SW_SPST_B3U-1000P

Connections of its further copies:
GND: R15.1; also elsewhere on the board
unnamed: R15.2, SW4.2
button_B: SW4.1; also elsewhere on the board

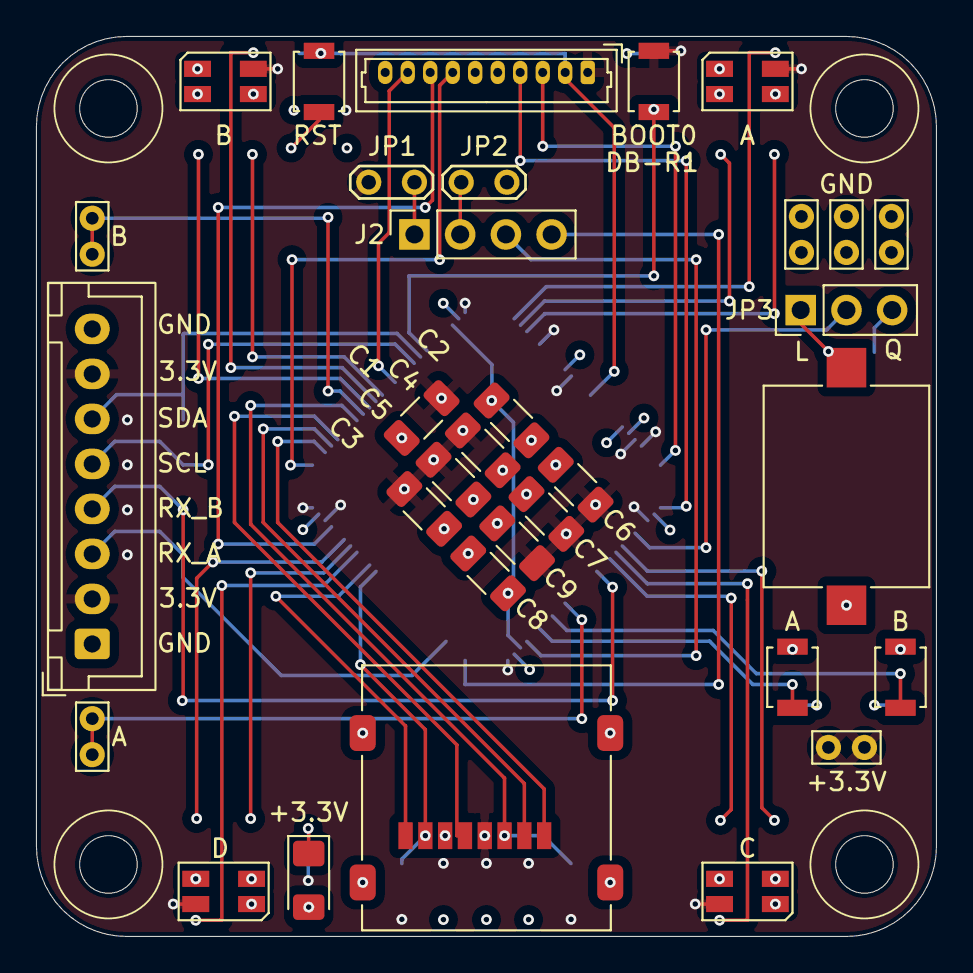
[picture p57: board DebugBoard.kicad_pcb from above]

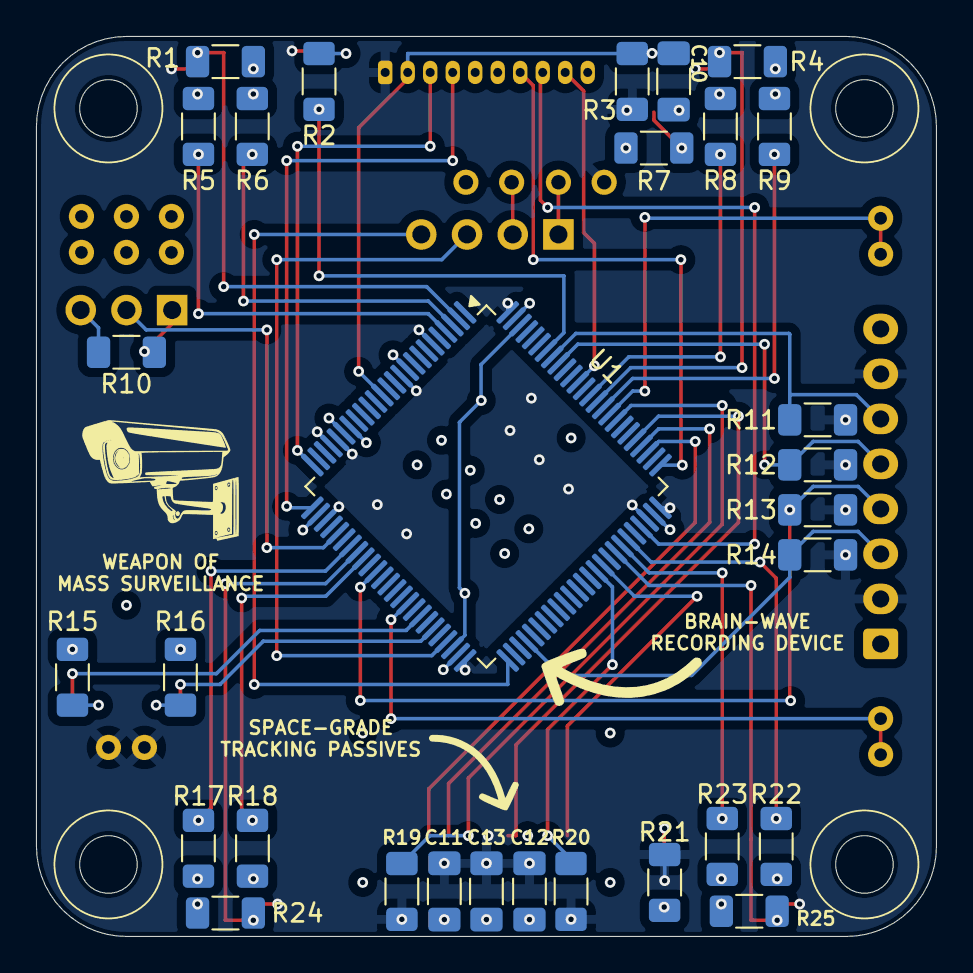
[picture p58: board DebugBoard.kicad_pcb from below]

Board: 4 copper layers, 50.0 x 50.0 mm, 66 parts (30 on the bottom side), 59 nets.

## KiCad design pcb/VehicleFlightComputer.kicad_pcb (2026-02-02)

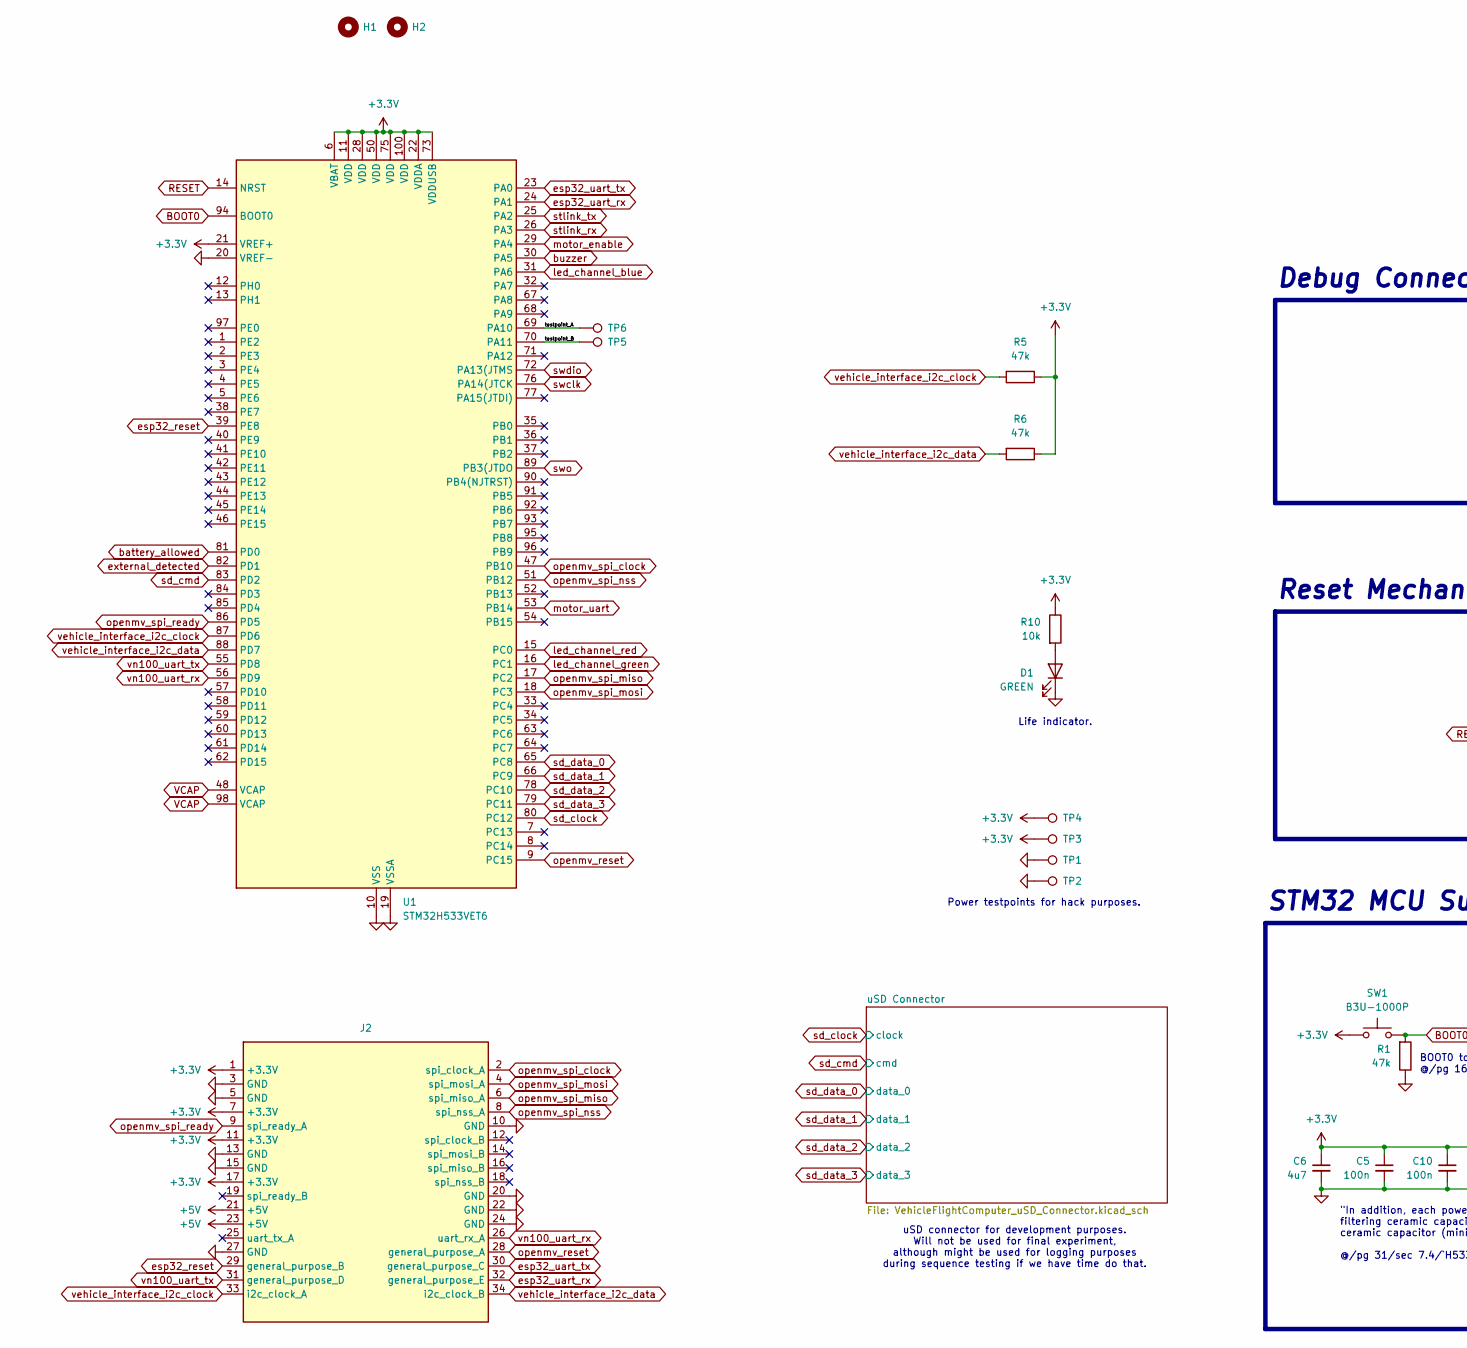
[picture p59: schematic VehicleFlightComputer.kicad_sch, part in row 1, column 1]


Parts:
BZ1: AST1109MLTRQ; Buzzer_Mallory_AST1109MLTRQ
C1, C3, C5, C7, C8, C10, C11: 100n; C_1206_3216Metric_Pad1.33x1.80mm_HandSolder
C4, C9: 2u2; C_1206_3216Metric_Pad1.33x1.80mm_HandSolder
C6: 4u7; C_1206_3216Metric_Pad1.33x1.80mm_HandSolder
D1: GREEN; LED_1206_3216Metric_Pad1.42x1.75mm_HandSolder
D2: 150141M173100; LED_RGB_Wuerth-PLCC4_3.2x2.8mm_150141M173100
H1, H2: MountingHole; MountingHole_3.2mm_M3
J1: XF3M_2415_1B
J2: VehicleStackConnector
J3: Debug; Molex_PicoBlade_53047-1010_1x10_P1.25mm_Vertical
JP1: Jumper_3_Bridged12; PinHeader_1x03_P2.54mm_Vertical
R1, R5, R6: 47k; R_1206_3216Metric_Pad1.30x1.75mm_HandSolder
R2, R10: 10k; R_1206_3216Metric_Pad1.30x1.75mm_HandSolder
R7, R8, R9: 2K; R_1206_3216Metric_Pad1.30x1.75mm_HandSolder
R11: 100; R_1206_3216Metric_Pad1.30x1.75mm_HandSolder
R12: 1K; R_1206_3216Metric_Pad1.30x1.75mm_HandSolder
SW1, SW2: B3U-1000P; SW_SPST_B3U-1000P
TP1, TP2, TP3, TP4, TP5, TP6: TestPoint; TestPoint_Bridge_Pitch2.0mm_Drill0.7mm
U1: STM32H533VET6; LQFP-100_14x14mm_P0.5mm

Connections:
+3.3V: C3.1, C5.1, C6.1, C7.1, C8.1, C10.1, C11.1, D2.1 (A), J1.6, J1.13, J1.19, J2.1 (+3.3V), J2.7 (+3.3V), J2.11 (+3.3V), J2.17 (+3.3V), J3.1, R5.1, R6.1, R10.1, R11.1, SW1.1, TP3.1, TP4.1, U1.6 (VBAT), U1.11 (VDD), U1.21 (VREF+), U1.22 (VDDA), U1.28 (VDD), U1.50 (VDD), U1.73 (VDDUSB), U1.75 (VDD), U1.100 (VDD); also elsewhere on the board
+5V: J1.11, J1.15, J2.21 (+5V), J2.23 (+5V)
/testpoint_A: TP6.1, U1.69 (PA10)
/testpoint_B: TP5.1, U1.70 (PA11)
BOOT0: R1.2, SW1.2, U1.94 (BOOT0)
GND: BZ1.2 (-), C1.2, C3.2, C4.2, C5.2, C6.2, C7.2, C8.2, C9.2, C10.2, C11.2, D1.1 (K), J1.1, J1.2, J1.10, J1.12, J1.14, J1.16, J1.23, J1.24, J2.3 (GND), J2.5 (GND), J2.10 (GND), J2.13 (GND), J2.15 (GND), J2.20 (GND), J2.22 (GND), J2.24 (GND), J2.27 (GND), J3.5, J3.6, J3.10, R1.1, R12.2, TP1.1, TP2.1, U1.10 (VSS), U1.19 (VSSA), U1.20 (VREF-), U1.27 (VSS), U1.49 (VSS), U1.74 (VSS), U1.99 (VSS); also elsewhere on the board
unnamed: BZ1.1 (+), JP1.1 (A), R2.2
unnamed: D1.2 (A), R10.2
unnamed: D2.2 (BK), R7.1
unnamed: D2.4 (GK), R9.1
unnamed: D2.3 (RK), R8.1
unnamed: JP1.3 (B), R2.1
unnamed: R12.1, SW2.2
RESET: C1.1, J3.2, R11.2, SW2.1, U1.14 (NRST)
VCAP: C4.1, C9.1, U1.48 (VCAP), U1.98 (VCAP)
battery_allowed: J1.18, U1.81 (PD0)
buzzer: JP1.2 (C), U1.30 (PA5)
esp32_reset: J2.29 (general_purpose_B), U1.39 (PE8)
esp32_uart_rx: J2.32 (general_purpose_E), U1.24 (PA1)
esp32_uart_tx: J2.30 (general_purpose_C), U1.23 (PA0)
external_detected: J1.17, U1.82 (PD1)
led_channel_blue: R7.2, U1.31 (PA6)
led_channel_green: R9.2, U1.16 (PC1)
led_channel_red: R8.2, U1.15 (PC0)
motor_enable: J1.7, U1.29 (PA4)
motor_uart: J1.9, U1.53 (PB14)
openmv_reset: J2.28 (general_purpose_A), U1.9 (PC15)
openmv_spi_clock: J2.2 (spi_clock_A), U1.47 (PB10)
openmv_spi_miso: J2.6 (spi_miso_A), U1.17 (PC2)
openmv_spi_mosi: J2.4 (spi_mosi_A), U1.18 (PC3)
openmv_spi_nss: J2.8 (spi_nss_A), U1.51 (PB12)
openmv_spi_ready: J2.9 (spi_ready_A), U1.86 (PD5)
sd_clock: U1.80 (PC12); also elsewhere on the board
sd_cmd: U1.83 (PD2); also elsewhere on the board
sd_data_0: U1.65 (PC8); also elsewhere on the board
sd_data_1: U1.66 (PC9); also elsewhere on the board
sd_data_2: U1.78 (PC10); also elsewhere on the board
sd_data_3: U1.79 (PC11); also elsewhere on the board
stlink_rx: J3.4, U1.26 (PA3)
stlink_tx: J3.3, U1.25 (PA2)
swclk: J3.7, U1.76 (PA14(JTCK)
swdio: J3.8, U1.72 (PA13(JTMS)
swo: J3.9, U1.89 (PB3(JTDO)
vehicle_interface_i2c_clock: J2.33 (i2c_clock_A), R5.2, U1.87 (PD6)
vehicle_interface_i2c_data: J2.34 (i2c_clock_B), R6.2, U1.88 (PD7)
vn100_uart_rx: J2.26 (uart_rx_A), U1.56 (PD9)
vn100_uart_tx: J2.31 (general_purpose_D), U1.55 (PD8)

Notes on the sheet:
Pin ordering should account for backwards connection.
STM32 MCU Support (V1 : Smaller BOOT0 setting).
Life indicator.
Reset Mechanism (V4 : Removed local-net).
Debug Connector (V2 : Removed To-Do).
BOOT0 to GND has MCU boot from flash. @/pg 163/tbl 15/`H533rm`.
uSD connector for development purposes. Will not be used for final experiment, although might be used for logging purposes during sequence testing if we have time do that.
"If there are two VCAP pins (such as for the LQFP64 package), each pin must be connected to a 2.2uF (typical) capacitor (for a total approximately 4.4 uF)." @/pg 35/sec 8.2/`H533an`. @/pg 12/fig 6/`H533an`. @/pg 34/fig 14/`H533an`.
Vehicle PDS I/O (V8 : Removed footprint).
Power testpoints for hack purposes.
"In addition, each power supply pair should be decoupled with filtering ceramic capacitors (100 nF) and one single ceramic capacitor (minimum 4.7 uF) connected in parallel." @/pg 31/sec 7.4/`H533an`.
"If no external battery is used in the application, it is recommended to connect VBAT externally to VDD with a 100 nF external ceramic decoupling capacitor." @/pg 7/sec 2.1.4/`H533an`. "[VDDA] must be connected to VDD when these [analog] peripherals are not used." "[VDDUSB] must preferably be conne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
Debug Buzzer (V7 : Simplified).
Debug LED (V5 : Removed local nets).


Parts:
C2: 100n; C_1206_3216Metric_Pad1.33x1.80mm_HandSolder
C12: 10n; C_1206_3216Metric_Pad1.33x1.80mm_HandSolder
C13: 1u; C_1206_3216Metric_Pad1.33x1.80mm_HandSolder
J4: 0472192001; microSD_HC_Molex_47219-2001
R3, R4: 10k; R_1206_3216Metric_Pad1.30x1.75mm_HandSolder

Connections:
+3.3V: C2.1, C12.1, C13.1, J4.4 (VDD), R3.1, R4.1; also elsewhere on the board
GND: C2.2, C12.2, C13.2, J4.6 (VSS), J4.9 (SHIELD); also elsewhere on the board
sd_clock: J4.5 (CLK); also elsewhere on the board
sd_cmd: J4.3 (CMD), R4.2; also elsewhere on the board
sd_data_0: J4.7 (DAT0), R3.2; also elsewhere on the board
sd_data_1: J4.8 (DAT1); also elsewhere on the board
sd_data_2: J4.1 (DAT2); also elsewhere on the board
sd_data_3: J4.2 (DAT3/CD); also elsewhere on the board

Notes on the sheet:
uSD Connector (V8 : Pull-up resistors).



Board: 4 copper layers, 50.0 x 50.0 mm, 45 parts (20 on the bottom side), 47 nets.

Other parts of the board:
N1: Housing; VehicleFlightComputerHousing

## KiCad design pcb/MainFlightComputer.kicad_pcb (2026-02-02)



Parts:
BZ1: AST1109MLTRQ; Buzzer_Mallory_AST1109MLTRQ
C1, C2, C3, C6, C7, C9, C11, C12, C13, C14: 100n; C_1206_3216Metric_Pad1.33x1.80mm_HandSolder
C4, C8: 2u2; C_1206_3216Metric_Pad1.33x1.80mm_HandSolder
C5: 4u7; C_1206_3216Metric_Pad1.33x1.80mm_HandSolder
C10: 220n; C_1206_3216Metric_Pad1.33x1.80mm_HandSolder
C15: 10u; C_1206_3216Metric_Pad1.33x1.80mm_HandSolder
C16: 100n; C_1206_3216Metric_Pad1.33x1.80mm_HandSolder; not fitted
D1: 150141M173100; LED_RGB_Wuerth-PLCC4_3.2x2.8mm_150141M173100
D6: GREEN; LED_1206_3216Metric_Pad1.42x1.75mm_HandSolder
J1: MainStackConnector
J3: Debug; Molex_PicoBlade_53047-1010_1x10_P1.25mm_Vertical
JP1: SolderJumper_3_Open; SolderJumper-3_P1.3mm_Open_RoundedPad1.0x1.5mm_NumberLabels
JP2: Jumper_3_Bridged12; PinHeader_1x03_P2.54mm_Vertical
R1, R2, R3: 2K; R_1206_3216Metric_Pad1.30x1.75mm_HandSolder
R4, R5, R6, R7, R8, R9, R12, R22: 10k; R_1206_3216Metric_Pad1.30x1.75mm_HandSolder
R10: 1K; R_1206_3216Metric_Pad1.30x1.75mm_HandSolder
R11: 100; R_1206_3216Metric_Pad1.30x1.75mm_HandSolder; not fitted
R13: 47k; R_1206_3216Metric_Pad1.30x1.75mm_HandSolder
SW1, SW2: B3U-1000P; SW_SPST_B3U-1000P
TP1, TP2, TP3, TP4, TP5, TP6, TP7, TP8: TestPoint; TestPoint_Bridge_Pitch2.0mm_Drill0.7mm
U1: STM32H533VET6; LQFP-100_14x14mm_P0.5mm
U2: LIS2MDL; LGA-12_2x2mm_P0.5mm
U3: LSM6DSV32X; LGA-14_3x2.5mm_P0.5mm_LayoutBorder3x4y

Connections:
+3.3V: C1.1, C2.1, C3.1, C5.1, C6.1, C7.1, C9.1, C11.1, C12.1, C13.1, C14.1, C15.1, D1.1 (A), J1.1 (+3.3V), J1.7 (+3.3V), J1.11 (+3.3V), J1.17 (+3.3V), J1.21 (+3.3V), J1.27 (+3.3V), J1.31 (+3.3V), J1.37 (+3.3V), J3.1, JP1.3 (B), R4.2, R5.2, R6.2, R7.2, R8.2, R9.2, R11.1, R22.1, SW2.1, TP1.1, TP2.1, U1.6 (VBAT), U1.11 (VDD), U1.21 (VREF+), U1.22 (VDDA), U1.28 (VDD), U1.50 (VDD), U1.73 (VDDUSB), U1.75 (VDD), U1.100 (VDD), U2.9 (Vdd), U2.10 (Vdd_IO), U3.5 (Vdd_IO), U3.8 (Vdd); also elsewhere on the board
/testpoint_A: TP5.1, U1.42 (PE11)
/testpoint_B: TP7.1, U1.35 (PB0)
/testpoint_C: TP6.1, U1.34 (PC5)
/testpoint_D: TP8.1, U1.12 (PH0)
BOOT0: R13.2, SW2.2, U1.94 (BOOT0)
GND: BZ1.2 (-), C1.2, C2.2, C3.2, C4.2, C5.2, C6.2, C7.2, C8.2, C9.2, C10.2, C11.2, C12.2, C13.2, C14.2, C15.2, C16.2, D6.1 (K), J1.3 (GND), J1.5 (GND), J1.10 (GND), J1.14 (GND), J1.20 (GND), J1.23 (GND), J1.25 (GND), J1.30 (GND), J1.34 (GND), J1.40 (GND), J3.5, J3.6, J3.10, JP1.1 (A), R10.2, R13.1, TP3.1, TP4.1, U1.10 (VSS), U1.19 (VSSA), U1.20 (VREF-), U1.27 (VSS), U1.49 (VSS), U1.74 (VSS), U1.99 (VSS), U2.6 (GND), U2.8 (GND), U3.2 (SDx/AH1/Qvar1), U3.3 (SCx/AH2/Qvar2), U3.6 (GND), U3.7 (GND); also elsewhere on the board
unnamed: BZ1.1 (+), JP2.1 (A), R12.2
unnamed: D1.2 (BK), R3.1
unnamed: D1.4 (GK), R1.1
unnamed: D1.3 (RK), R2.1
unnamed: D6.2 (A), R22.2
unnamed: JP1.2 (C), U3.1 (SDO/SA0)
unnamed: JP2.3 (B), R12.1
unnamed: R10.1, SW1.2
unnamed: C10.1, U2.5 (C1)
RESET: C16.1, J3.2, R11.2, SW1.1, U1.14 (NRST)
VCAP: C4.1, C8.1, U1.48 (VCAP), U1.98 (VCAP)
buzzer: JP2.2 (C), U1.63 (PC6)
esp32_reset: J1.15 (general_purpose_A), U1.57 (PD10)
esp32_uart_rx: J1.13 (uart_rx_A), U1.54 (PB15)
esp32_uart_tx: J1.12 (uart_tx_A), U1.53 (PB14)
flight_computer_debug_i2c_clock: J1.38 (i2c_clock_B), R6.1, U1.87 (PD6)
flight_computer_debug_i2c_data: J1.39 (i2c_data_B), R7.1, U1.88 (PD7)
general_purpose_B: J1.16 (general_purpose_B), U1.59 (PD12)
general_purpose_C: J1.35 (general_purpose_C), U1.15 (PC0)
general_purpose_D: J1.36 (general_purpose_D), U1.9 (PC15)
general_purpose_G: J1.43 (general_purpose_G), U1.8 (PC14)
general_purpose_H: J1.44 (general_purpose_H), U1.7 (PC13)
general_purpose_I: J1.45 (general_purpose_I), U1.5 (PE6)
general_purpose_J: J1.46 (general_purpose_J), U1.84 (PD3)
general_purpose_K: J1.47 (general_purpose_K), U1.82 (PD1)
general_purpose_N: J1.50 (general_purpose_N), U1.97 (PE0)
led_channel_blue: R3.2, U1.3 (PE4)
led_channel_green: R1.2, U1.2 (PE3)
led_channel_red: R2.2, U1.1 (PE2)
lis2mdl_chip_select: U1.61 (PD14), U2.3 (~CS)
lis2mdl_data_ready: U1.44 (PE13), U2.7 (DRDY)
logic_gse_1: J1.48 (general_purpose_L), U1.85 (PD4)
logic_timer_event_1: J1.49 (general_purpose_M), U1.96 (PB9)
lsm6dsv32x_chip_select: U1.45 (PE14), U3.12 (CS)
lsm6dsv32x_interrupt_1: U1.71 (PA12), U3.4 (INT1)
lsm6dsv32x_interrupt_2: U1.64 (PC7), U3.9 (INT2)
sd_clock: U1.80 (PC12); also elsewhere on the board
sd_cmd: U1.83 (PD2); also elsewhere on the board
sd_data_0: U1.65 (PC8); also elsewhere on the board
sd_data_1: U1.66 (PC9); also elsewhere on the board
sd_data_2: U1.78 (PC10); also elsewhere on the board
sd_data_3: U1.79 (PC11); also elsewhere on the board
sensor_i2c_clock: R8.1, U1.47 (PB10), U2.1 (SCL/SPC), U3.13 (SCL)
sensor_i2c_data: R9.1, U1.51 (PB12), U2.4 (SDA/SDI/SDO), U3.14 (SDA)
solarboard_analog_A: J1.41 (general_purpose_E), U1.23 (PA0)
solarboard_analog_B: J1.42 (general_purpose_F), U1.24 (PA1)
spi_clock_A: J1.2 (spi_clock_A), U1.52 (PB13)
spi_clock_B: J1.22 (spi_clock_B), U1.30 (PA5)
spi_miso_A: J1.6 (spi_miso_A), U1.17 (PC2)
spi_miso_B: J1.26 (spi_miso_B), U1.31 (PA6)
spi_mosi_A: J1.4 (spi_mosi_A), U1.16 (PC1)
spi_mosi_B: J1.24 (spi_mosi_B), U1.91 (PB5)
spi_nss_A: J1.8 (spi_nss_A), U1.70 (PA11)
spi_nss_B: J1.28 (spi_nss_B), U1.29 (PA4)
spi_ready_A: J1.9 (spi_ready_A), U1.86 (PD5)
spi_ready_B: J1.29 (spi_ready_B), U1.37 (PB2)
stlink_rx: J3.4, U1.26 (PA3)
stlink_tx: J3.3, U1.25 (PA2)
swclk: J3.7, U1.76 (PA14(JTCK)
swdio: J3.8, U1.72 (PA13(JTMS)
swo: J3.9, U1.89 (PB3(JTDO)
uart_rx_B: J1.33 (uart_rx_B), U1.36 (PB1)
uart_tx_B: J1.32 (uart_tx_B), U1.55 (PD8)
vehicle_interface_i2c_clock: J1.18 (i2c_clock_A), R4.1, U1.92 (PB6)
vehicle_interface_i2c_data: J1.19 (i2c_data_A), R5.1, U1.93 (PB7)

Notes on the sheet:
STM32 MCU Support (V1 : Smaller BOOT0 setting).
Life indicator.
"Interrupt/data-ready signal." @/pg 9/tbl 8/`LIS2MDL`.
Reset Mechanism (V4 : Removed local-net).
The sensor seems to be fine running at 3.3V. @/pg 14/tbl 4/`LSM6DSV32X`. @/pg 47/fig 28/`LSM6DSV32X`.
Debug Connector (V2 : Removed To-Do).
The sensor seems to be fine running at 3.3V. @/pg 9/tbl 8/`LIS2MDL`. @/pg 13/fig 5/`LIS2MDL`.
Test-points for measurements and hacks.
BOOT0 to GND has MCU boot from flash. @/pg 163/tbl 15/`H533rm`.
"GND or Vdd_IO". @/pg 47/fig 28/`LSM6DSV32X`.
"If there are two VCAP pins (such as for the LQFP64 package), each pin must be connected to a 2.2uF (typical) capacitor (for a total approximately 4.4 uF)." @/pg 35/sec 8.2/`H533an`. @/pg 12/fig 6/`H533an`. @/pg 34/fig 14/`H533an`.
The LSM6DSV32X will be configured in mode 1. @/pg 10/fig 6/`LSM6DSV32X`.
"Capacitor connection (C1 = 220 nF)". @/pg 3/tbl 1/`LIS2MDL`. @/pg 13/fig 5/`LIS2MDL`.
"Leave pin electrically unconnected and soldered to PCB." @/pg 47/fig 28/`LSM6DSV32X`.
"In addition, each power supply pair should be decoupled with filtering ceramic capacitors (100 nF) and one single ceramic capacitor (minimum 4.7 uF) connected in parallel." @/pg 31/sec 7.4/`H533an`.
"If no external battery is used in the application, it is recommended to connect VBAT externally to VDD with a 100 nF external ceramic decoupling capacitor." @/pg 7/sec 2.1.4/`H533an`. "[VDDA] must be connected to VDD when these [analog] peripherals are not used." "[VDDUSB] must preferably be conne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
Debug Buzzer (V7 : Simplified).
Debug LED (V5 : Removed local nets).
"I2C least significant bit of the device address (SA0)". @/pg 11/tbl 2/`LSM6DSV32X`.

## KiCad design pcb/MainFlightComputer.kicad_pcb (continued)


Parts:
C17: 10n; C_1206_3216Metric_Pad1.33x1.80mm_HandSolder
C18: 100n; C_1206_3216Metric_Pad1.33x1.80mm_HandSolder
C19: 1u; C_1206_3216Metric_Pad1.33x1.80mm_HandSolder
J2: 0472192001; microSD_HC_Molex_47219-2001
R14, R15: 10k; R_1206_3216Metric_Pad1.30x1.75mm_HandSolder

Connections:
+3.3V: C17.1, C18.1, C19.1, J2.4 (VDD), R14.1, R15.1; also elsewhere on the board
GND: C17.2, C18.2, C19.2, J2.6 (VSS), J2.9 (SHIELD); also elsewhere on the board
sd_clock: J2.5 (CLK); also elsewhere on the board
sd_cmd: J2.3 (CMD), R15.2; also elsewhere on the board
sd_data_0: J2.7 (DAT0), R14.2; also elsewhere on the board
sd_data_1: J2.8 (DAT1); also elsewhere on the board
sd_data_2: J2.1 (DAT2); also elsewhere on the board
sd_data_3: J2.2 (DAT3/CD); also elsewhere on the board

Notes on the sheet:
uSD Connector (V8 : Pull-up resistors).



Board: 4 copper layers, 66.0 x 60.0 mm, 57 parts (35 on the bottom side), 72 nets.

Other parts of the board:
N1: Housing; MainFlightComputerHousing

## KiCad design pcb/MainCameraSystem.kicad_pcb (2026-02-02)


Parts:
C4: 100n; C_1206_3216Metric_Pad1.33x1.80mm_HandSolder; not fitted
C5, C6, C7, C8, C13, C14, C17: 100n; C_1206_3216Metric_Pad1.33x1.80mm_HandSolder
C9: 4u7; C_1206_3216Metric_Pad1.33x1.80mm_HandSolder
C10, C11, C21: 10u; C_1206_3216Metric_Pad1.33x1.80mm_HandSolder
C12, C15: 2u2; C_1206_3216Metric_Pad1.33x1.80mm_HandSolder
C16, C18, C20: 1u; C_1206_3216Metric_Pad1.33x1.80mm_HandSolder
C19: 10n; C_1206_3216Metric_Pad1.33x1.80mm_HandSolder
C22: 22p; C_1206_3216Metric_Pad1.33x1.80mm_HandSolder
D1: 150141M173100; LED_RGB_Wuerth-PLCC4_3.2x2.8mm_150141M173100
FB1: Ferrite; L_1206_3216Metric_Pad1.22x1.90mm_HandSolder
H1, H2, H3, H4: MountingHole; MountingHole_3.2mm_M3
J1: Debug; Molex_PicoBlade_53047-1010_1x10_P1.25mm_Vertical
J2: B8B-XH-A; JST_XH_B8B-XH-A_1x08_P2.50mm_Vertical
J3: XF3M_2415_1B; XF3M_2415_1B - REVERSED
R1, R2, R9: 2K; R_1206_3216Metric_Pad1.30x1.75mm_HandSolder
R3: 47k; R_1206_3216Metric_Pad1.30x1.75mm_HandSolder
R4: 100; R_1206_3216Metric_Pad1.30x1.75mm_HandSolder; not fitted
R7: 1K; R_1206_3216Metric_Pad1.30x1.75mm_HandSolder
R8, R10, R11, R12: 10k; R_1206_3216Metric_Pad1.30x1.75mm_HandSolder
SW1, SW2: B3U-1000P; SW_SPST_B3U-1000P
TP1, TP2: TestPoint; TestPoint_Bridge_Pitch2.0mm_Drill0.7mm
U1: STM32H533VET6; LQFP-100_14x14mm_P0.5mm
U2: AP2127N-2.8TRG1; SOT-23-3
U3: AP2127N-1.5TRG1; SOT-23
Y1: ASV-24.000MHZ-EJ-T; Oscillator_SMD_Abracon_ASV-4Pin_7.0x5.1mm

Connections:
+1V5: C20.1, C21.1, J3.10, U3.2 (VO)
+2V8: C10.1, C16.1, J3.4, U2.2 (VO)
+3.3V: C5.1, C6.1, C7.1, C8.1, C9.1, C11.1, C13.1, C14.1, C18.1, C19.1, D1.1 (A), J1.1, J2.2, J3.11, R4.1, R8.1, R10.1, R11.1, SW2.1, U1.6 (VBAT), U1.11 (VDD), U1.21 (VREF+), U1.22 (VDDA), U1.28 (VDD), U1.50 (VDD), U1.73 (VDDUSB), U1.75 (VDD), U1.100 (VDD), U2.3 (VI), U3.3 (VI), Y1.1 (EN), Y1.4 (Vdd); also elsewhere on the board
/testpoint_A: TP1.1, U1.88 (PD7)
/testpoint_B: TP2.1, U1.68 (PA9)
BOOT0: R3.2, SW2.2, U1.94 (BOOT0)
GND: C4.2, C5.2, C6.2, C7.2, C8.2, C9.2, C10.2, C11.2, C12.2, C13.2, C14.2, C15.2, C16.2, C17.2, C18.2, C19.2, C20.2, C21.2, C22.2, FB1.1, J1.5, J1.6, J1.10, J2.1, J3.15, R3.1, R7.2, R12.2, U1.10 (VSS), U1.19 (VSSA), U1.20 (VREF-), U1.27 (VSS), U1.49 (VSS), U1.74 (VSS), U1.99 (VSS), U2.1 (GND), U3.1 (GND), Y1.2 (GND); also elsewhere on the board
GNDA: FB1.2, J3.2
unnamed: D1.2 (BK), R2.1
unnamed: D1.4 (GK), R9.1
unnamed: D1.3 (RK), R1.1
unnamed: R7.1, SW1.2
OV_XCLK: J3.13, Y1.3 (OUT)
RESET: C4.1, J1.2, R4.2, SW1.1, U1.14 (NRST)
VCAP: C12.1, C15.1, U1.48 (VCAP), U1.98 (VCAP)
led_channel_blue: R2.2, U1.37 (PB2)
led_channel_green: R9.2, U1.36 (PB1)
led_channel_red: R1.2, U1.38 (PE7)
ovcam_hsync: J3.9, U1.29 (PA4)
ovcam_i2c_clock: J3.5, R10.2, U1.47 (PB10)
ovcam_i2c_data: J3.3, R11.2, U1.51 (PB12)
ovcam_pixel_clock: C22.1, J3.17, U1.31 (PA6)
ovcam_power_down: J3.8, R12.1, U1.30 (PA5)
ovcam_reset: C17.1, J3.6, R8.2, U1.5 (PE6)
ovcam_vsync: J3.7, U1.93 (PB7)
ovcam_y2: J3.19, U1.63 (PC6)
ovcam_y3: J3.21, U1.64 (PC7)
ovcam_y4: J3.22, U1.54 (PB15)
ovcam_y5: J3.20, U1.1 (PE2)
ovcam_y6: J3.18, U1.3 (PE4)
ovcam_y7: J3.16, U1.92 (PB6)
ovcam_y8: J3.14, U1.95 (PB8)
ovcam_y9: J3.12, U1.90 (PB4(NJTRST))
sd_clock: J2.6, U1.80 (PC12); also elsewhere on the board
sd_cmd: J2.5, U1.83 (PD2); also elsewhere on the board
sd_data_0: J2.3, U1.65 (PC8); also elsewhere on the board
sd_data_1: J2.4, U1.66 (PC9); also elsewhere on the board
sd_data_2: J2.8, U1.78 (PC10); also elsewhere on the board
sd_data_3: J2.7, U1.79 (PC11); also elsewhere on the board
stlink_rx: J1.4, U1.26 (PA3)
stlink_tx: J1.3, U1.25 (PA2)
swclk: J1.7, U1.76 (PA14(JTCK)
swdio: J1.8, U1.72 (PA13(JTMS)
swo: J1.9, U1.89 (PB3(JTDO)

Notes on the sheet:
STM32 MCU Support (V1 : Smaller BOOT0 setting).
TODO: Look into overclocking the OV5640.
Reset Mechanism (V4 : Removed local-net).
Debug Connector (V2 : Removed To-Do).
Pin 23 is called AFVDD or also "Data 1". Adafruit has this as an optional feature. Pin 24 is unused but is also labelled as "Data 0" by Adafruit.
The data pin numbering begins at 2.
BOOT0 to GND has MCU boot from flash. @/pg 163/tbl 15/`H533rm`.
Adafruit says that pin 1 is also used for STROBE, but otherwise is an optional feature.
@/url:`https://github.com/adafruit/Adafruit-OV5640-Camera-Breakout-PCB`. @/url:`https://cdn-shop.adafruit.com/product-files/5839/C19938-001+datasheet+FD5640+-120D-AF-Model.pdf`.
Adafruit has unspecified ferrite value here. We very likely can get away with shorting this.
"If there are two VCAP pins (such as for the LQFP64 package), each pin must be connected to a 2.2uF (typical) capacitor (for a total approximately 4.4 uF)." @/pg 35/sec 8.2/`H533an`. @/pg 12/fig 6/`H533an`. @/pg 34/fig 14/`H533an`.
"In addition, each power supply pair should be decoupled with filtering ceramic capacitors (100 nF) and one single ceramic capacitor (minimum 4.7 uF) connected in parallel." @/pg 31/sec 7.4/`H533an`.
"If no external battery is used in the application, it is recommended to connect VBAT externally to VDD with a 100 nF external ceramic decoupling capacitor." @/pg 7/sec 2.1.4/`H533an`. "[VDDA] must be connected to VDD when these [analog] peripherals are not used." "[VDDUSB] must preferably be conne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
The onboard uSD connector is just for development purposes.
Debug LED (V5 : Removed local nets).


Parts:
C1: 1u; C_1206_3216Metric_Pad1.33x1.80mm_HandSolder
C2: 100n; C_1206_3216Metric_Pad1.33x1.80mm_HandSolder
C3: 10n; C_1206_3216Metric_Pad1.33x1.80mm_HandSolder
J4: 0472192001; microSD_HC_Molex_47219-2001
R5, R6: 10k; R_1206_3216Metric_Pad1.30x1.75mm_HandSolder

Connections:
+3.3V: C1.1, C2.1, C3.1, J4.4 (VDD), R5.1, R6.1; also elsewhere on the board
GND: C1.2, C2.2, C3.2, J4.6 (VSS), J4.9 (SHIELD); also elsewhere on the board
sd_clock: J4.5 (CLK); also elsewhere on the board
sd_cmd: J4.3 (CMD), R6.2; also elsewhere on the board
sd_data_0: J4.7 (DAT0), R5.2; also elsewhere on the board
sd_data_1: J4.8 (DAT1); also elsewhere on the board
sd_data_2: J4.1 (DAT2); also elsewhere on the board
sd_data_3: J4.2 (DAT3/CD); also elsewhere on the board

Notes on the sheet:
uSD Connector (V8 : Pull-up resistors).



Board: 4 copper layers, 40.0 x 40.0 mm, 52 parts (34 on the bottom side), 44 nets.

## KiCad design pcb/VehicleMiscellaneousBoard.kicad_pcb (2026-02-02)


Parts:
J1: VehicleStackConnector
J2: Conn_02x05_Top_Bottom; JST_XH_S10B-XH-A_1x10_P2.50mm_Horizontal
J4: B8B-XH-A; JST_XH_B8B-XH-A_1x08_P2.50mm_Vertical
U1: OpenMV H7+; OpenMV_H7_Plus
U2: Seeed_Studio_XIAO-ESP32-S3-Sense; Seeed_Studio_XIAO_ESP32_S3

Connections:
+3.3V: J1.1 (+3.3V), J1.7 (+3.3V), J1.11 (+3.3V), J1.17 (+3.3V), J4.1, J4.5, J4.7, U1.+3.3V, U2.+3.3V
+5V: J1.21 (+5V), J1.23 (+5V), J2.1, J2.3
GND: J1.3 (GND), J1.5 (GND), J1.10 (GND), J1.13 (GND), J1.15 (GND), J1.20 (GND), J1.22 (GND), J1.24 (GND), J1.27 (GND), J2.2, J2.4, J4.4, J4.6, J4.8, U1.GND, U2.GND
esp32_reset: J1.29 (general_purpose_B), U2.EN
esp32_uart_rx: J1.32 (general_purpose_E), U2.D6
esp32_uart_tx: J1.30 (general_purpose_C), U2.D7
openmv_reset: J1.28 (general_purpose_A), U1.NRST
openmv_spi_clock: J1.2 (spi_clock_A), U1.PB13
openmv_spi_miso: J1.6 (spi_miso_A), U1.PB14
openmv_spi_mosi: J1.4 (spi_mosi_A), U1.PB15
openmv_spi_nss: J1.8 (spi_nss_A), U1.PB12
openmv_spi_ready: J1.9 (spi_ready_A), U1.PD13
vehicle_interface_i2c_clock: J1.33 (i2c_clock_A), J4.2
vehicle_interface_i2c_data: J1.34 (i2c_clock_B), J4.3
vn100_uart_rx: J1.26 (uart_rx_A), J2.8
vn100_uart_tx: J1.31 (general_purpose_D), J2.9



Board: 4 copper layers, 50.0 x 50.0 mm, 6 parts (3 on the bottom side), 16 nets.

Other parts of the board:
N1: Housing; Dummy

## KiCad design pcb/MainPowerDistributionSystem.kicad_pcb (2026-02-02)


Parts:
C1, C2, C3, C4: 1u; C_1206_3216Metric_Pad1.33x1.80mm_HandSolder
C5, C7: ?; C_1206_3216Metric_Pad1.33x1.80mm_HandSolder; not fitted
C6: 22u; C_1206_3216Metric_Pad1.33x1.80mm_HandSolder
D5: RED; LED_1206_3216Metric_Pad1.42x1.75mm_HandSolder
D6: GREEN; LED_1206_3216Metric_Pad1.42x1.75mm_HandSolder
J1: Conn_02x05_Top_Bottom; JST_XH_S10B-XH-A_1x10_P2.50mm_Horizontal
J2: MainStackConnector
JP1: SolderJumper_2_Open; SolderJumper-2_P1.3mm_Open_RoundedPad1.0x1.5mm
R5, R6: 100k; R_1206_3216Metric_Pad1.30x1.75mm_HandSolder
R7: 910k; R_1206_3216Metric_Pad1.30x1.75mm_HandSolder
R8, R9, R11, R12, R13: ?; R_1206_3216Metric_Pad1.30x1.75mm_HandSolder; not fitted
R10: 360k; R_1206_3216Metric_Pad1.30x1.75mm_HandSolder
R14: 0; R_1206_3216Metric_Pad1.30x1.75mm_HandSolder
R15: 10k; R_1206_3216Metric_Pad1.30x1.75mm_HandSolder
TP1, TP2, TP3, TP4, TP5, TP6: TestPoint; TestPoint_Bridge_Pitch2.0mm_Drill0.7mm
U1, U2, U3: D24V7F3; D24V7Fx
U4: BTS462TATMA1; TO-252-4
U5: LM339; SOIC-14_3.9x8.7mm_P1.27mm

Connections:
+3.3V: C1.1, C2.1, C3.1, C4.1, D6.2 (A), J1.3, J1.7, J2.1 (+3.3V), J2.7 (+3.3V), J2.11 (+3.3V), J2.17 (+3.3V), J2.21 (+3.3V), J2.27 (+3.3V), J2.31 (+3.3V), J2.37 (+3.3V), R5.2, R14.2, TP3.1, TP4.1, U1.VOUT, U2.VOUT, U3.VOUT
+GSE-1: J1.1, TP2.1, U1.VIN, U2.VIN, U3.VIN; also elsewhere on the board
+TE-1: J1.9, R7.2, R8.2, R9.2, TP1.1, U4.3 (Vbb), U5.3 (V+); also elsewhere on the board
BURNWIRE_VOLTAGE: D5.2 (A), J1.5, U4.5 (OUT)
GND: C1.2, C2.2, C3.2, C4.2, C5.2, C6.2, C7.2, J1.2, J1.4, J1.6, J1.8, J1.10, J2.3 (GND), J2.5 (GND), J2.10 (GND), J2.14 (GND), J2.20 (GND), J2.23 (GND), J2.25 (GND), J2.30 (GND), J2.34 (GND), J2.40 (GND), R6.2, R10.1, R11.1, R12.1, R13.1, R15.2, TP5.1, TP6.1, U1.GND, U2.GND, U3.GND, U4.1 (GND), U5.12 (V-); also elsewhere on the board
unnamed: D5.1 (K), R6.1
unnamed: D6.1 (K), R15.1
unnamed: JP1.1 (A), U5.2
unnamed: JP1.2 (B), R5.1, U4.2 (IN)
unnamed: C5.1, C6.1, C7.1, R7.1, R8.1, R9.1, R10.2, R11.2, R12.2, U5.5 (+)
unnamed: R13.2, R14.1, U5.4 (-)
logic_gse_1: J2.48 (general_purpose_L); also elsewhere on the board
logic_timer_event_1: J2.49 (general_purpose_M); also elsewhere on the board

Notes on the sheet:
Multiple resistors in parallel to have a more specific voltage divider if needed.
Activation of the burn-wire will be determined by +TE-1. So as soon as +TE-1 gets set, the burn-wire should go off immediately. However, to prevent from +TE-1 being left on too long and risk damaging the burn-wire mechanism and circuitry, we have the load switches automatically cut off +TE-1 after 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
With burn-wire heating element as a 100 ohm resistor and +TE-1 expected to be at about 28V, we anticipate 28V / 100 ohm = 280 mA of current. This amounts to 280 mA * 28V = 7.84 W of power in the heating element. The BTS462TATMA1 is rated to handle up to 3.5A, so we should be good on that.
Multiple capacitors in parallel to have a more specific capacitance if needed.
If the burn-wire cut-off circuitry deems too much of a risk of a failed ejection, we should leave this solder jumper open.
Life indicator.
Honestly probably not useful to have logic converter for GSE-1 since that's what powers all of the experiment, but it's going to be left here for legacy reasons (i.e. laziness).
The main FC doesn't really do anything with +TE-1, but perhaps it could be a useful thing to log down as something that can be analyzed post-flight.
If needed, we can have a voltage divider here for the reference voltage to tune the cut-off time.
Test-points for measurements and hacks.
Each D24V7F3 should be able to handle 600mA, so with three in parallel, the main PDS should be able to support up to 1.8A of current draw. This would appear as about 0.2A through +GSE-1.

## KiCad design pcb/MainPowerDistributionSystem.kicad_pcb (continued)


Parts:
D1: WHITE; LED_1206_3216Metric_Pad1.42x1.75mm_HandSolder
D2: 1N4727A; D_A-405_P7.62mm_Horizontal
R1: 3k; R_1206_3216Metric_Pad1.30x1.75mm_HandSolder
R3: 100k; R_1206_3216Metric_Pad1.30x1.75mm_HandSolder

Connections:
+TE-1: D1.2 (A), R3.1; also elsewhere on the board
GND: D2.2 (A), R3.2; also elsewhere on the board
unnamed: D1.1 (K), R1.1
logic_timer_event_1: D2.1 (K), R1.2; also elsewhere on the board

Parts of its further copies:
D3: WHITE; LED_1206_3216Metric_Pad1.42x1.75mm_HandSolder
D4: 1N4727A; D_A-405_P7.62mm_Horizontal
R2: 3k; R_1206_3216Metric_Pad1.30x1.75mm_HandSolder
R4: 100k; R_1206_3216Metric_Pad1.30x1.75mm_HandSolder

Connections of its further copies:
+GSE-1: D3.2 (A), R4.1; also elsewhere on the board
GND: D4.2 (A), R4.2; also elsewhere on the board
unnamed: D3.1 (K), R2.1
logic_gse_1: D4.1 (K), R2.2; also elsewhere on the board

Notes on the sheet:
Timer Event Logic Conversion (V1 : Pull-down).
Acts as a drain for stray current.


Board: 2 copper layers, 66.0 x 60.0 mm, 43 parts (0 on the bottom side), 15 nets.

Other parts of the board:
N1: Housing; MainPowerDistributionSystemHousing

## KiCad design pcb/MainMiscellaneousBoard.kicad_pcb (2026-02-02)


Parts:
D1: GREEN; LED_1206_3216Metric_Pad1.42x1.75mm_HandSolder
J1, J2, J3, J4: B8B-XH-A; JST_XH_B8B-XH-A_1x08_P2.50mm_Vertical
J7: MainStackConnector
R5: 10k; R_1206_3216Metric_Pad1.30x1.75mm_HandSolder
TP1, TP2, TP3, TP4, TP5, TP6, TP7, TP8: TestPoint; TestPoint_Bridge_Pitch2.0mm_Drill0.7mm
U1: Seeed_Studio_XIAO-ESP32-S3-Sense; Seeed_Studio_XIAO_ESP32_S3

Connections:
+3.3V: J1.7, J2.1, J2.5, J3.1, J4.1, J7.1 (+3.3V), J7.7 (+3.3V), J7.11 (+3.3V), J7.17 (+3.3V), J7.21 (+3.3V), J7.27 (+3.3V), J7.31 (+3.3V), J7.37 (+3.3V), R5.1, TP7.1, TP8.1, U1.+3.3V; also elsewhere on the board
/general_purpose_G: J7.43 (general_purpose_G), TP2.1
/general_purpose_H: J7.44 (general_purpose_H), TP1.1
/general_purpose_I: J7.45 (general_purpose_I), TP3.1
/general_purpose_J: J7.46 (general_purpose_J), TP4.1
GND: D1.1 (K), J1.2, J1.4, J1.8, J2.4, J2.8, J3.2, J4.2, J7.3 (GND), J7.5 (GND), J7.10 (GND), J7.14 (GND), J7.20 (GND), J7.23 (GND), J7.25 (GND), J7.30 (GND), J7.34 (GND), J7.40 (GND), TP5.1, TP6.1, U1.GND; also elsewhere on the board
unnamed: D1.2 (A), R5.2
camera_A_sd_clock: J3.6; also elsewhere on the board
camera_A_sd_cmd: J3.5; also elsewhere on the board
camera_A_sd_data_0: J3.7; also elsewhere on the board
camera_A_sd_data_1: J3.8; also elsewhere on the board
camera_A_sd_data_2: J3.3; also elsewhere on the board
camera_A_sd_data_3: J3.4; also elsewhere on the board
camera_B_sd_clock: J4.6; also elsewhere on the board
camera_B_sd_cmd: J4.5; also elsewhere on the board
camera_B_sd_data_0: J4.7; also elsewhere on the board
camera_B_sd_data_1: J4.8; also elsewhere on the board
camera_B_sd_data_2: J4.3; also elsewhere on the board
camera_B_sd_data_3: J4.4; also elsewhere on the board
esp32_reset: J7.15 (general_purpose_A), U1.EN
esp32_uart_rx: J7.13 (uart_rx_A), U1.D6
esp32_uart_tx: J7.12 (uart_tx_A), U1.D7
flight_computer_debug_i2c_clock: J2.2, J7.38 (i2c_clock_B)
flight_computer_debug_i2c_data: J2.3, J7.39 (i2c_data_B)
solarboard_analog_A: J1.1, J7.41 (general_purpose_E)
solarboard_analog_B: J1.3, J7.42 (general_purpose_F)
uart_rx_B: J1.6, J7.33 (uart_rx_B)
uart_tx_B: J1.5, J7.32 (uart_tx_B)
vehicle_interface_i2c_clock: J2.6, J7.18 (i2c_clock_A)
vehicle_interface_i2c_data: J2.7, J7.19 (i2c_data_A)

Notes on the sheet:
Test-points for measurements and hacks.
Life indicator.
UART might be used for debug board.


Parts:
C4: 100n; C_1206_3216Metric_Pad1.33x1.80mm_HandSolder
C5: 1u; C_1206_3216Metric_Pad1.33x1.80mm_HandSolder
C6: 10n; C_1206_3216Metric_Pad1.33x1.80mm_HandSolder
J5: 0472192001; microSD_HC_Molex_47219-2001
R3, R4: 10k; R_1206_3216Metric_Pad1.30x1.75mm_HandSolder

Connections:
+3.3V: C4.1, C5.1, C6.1, J5.4 (VDD), R3.1, R4.1; also elsewhere on the board
GND: C4.2, C5.2, C6.2, J5.6 (VSS), J5.9 (SHIELD); also elsewhere on the board
camera_A_sd_clock: J5.5 (CLK); also elsewhere on the board
camera_A_sd_cmd: J5.3 (CMD), R3.2; also elsewhere on the board
camera_A_sd_data_0: J5.7 (DAT0), R4.2; also elsewhere on the board
camera_A_sd_data_1: J5.8 (DAT1); also elsewhere on the board
camera_A_sd_data_2: J5.1 (DAT2); also elsewhere on the board
camera_A_sd_data_3: J5.2 (DAT3/CD); also elsewhere on the board

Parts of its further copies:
C1: 1u; C_1206_3216Metric_Pad1.33x1.80mm_HandSolder
C2: 100n; C_1206_3216Metric_Pad1.33x1.80mm_HandSolder
C3: 10n; C_1206_3216Metric_Pad1.33x1.80mm_HandSolder
J6: 0472192001; microSD_HC_Molex_47219-2001
R1, R2: 10k; R_1206_3216Metric_Pad1.30x1.75mm_HandSolder

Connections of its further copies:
+3.3V: C1.1, C2.1, C3.1, J6.4 (VDD), R1.1, R2.1; also elsewhere on the board
GND: C1.2, C2.2, C3.2, J6.6 (VSS), J6.9 (SHIELD); also elsewhere on the board
camera_B_sd_clock: J6.5 (CLK); also elsewhere on the board
camera_B_sd_cmd: J6.3 (CMD), R2.2; also elsewhere on the board
camera_B_sd_data_0: J6.7 (DAT0), R1.2; also elsewhere on the board
camera_B_sd_data_1: J6.8 (DAT1); also elsewhere on the board
camera_B_sd_data_2: J6.1 (DAT2); also elsewhere on the board
camera_B_sd_data_3: J6.2 (DAT3/CD); also elsewhere on the board

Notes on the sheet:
uSD Connector (V8 : Pull-up resistors).



Board: 4 copper layers, 66.0 x 60.0 mm, 29 parts (11 on the bottom side), 30 nets.

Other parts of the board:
N1: Housing; MainMiscellaneousBoardHousing

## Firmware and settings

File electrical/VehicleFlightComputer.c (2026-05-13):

#define STEPPER_ENABLE_DELAY_US          500'000
#define STEPPER_VELOCITY_UPDATE_US       20'000 // @/`Sequence Angular Accelerations Delta Time`.
#define STEPPER_UART_TIME_MARGIN_US      2'000
#define STEPPER_RING_BUFFER_LENGTH       8
#define SPI_BLOCK_SIZE                   64     // @/`OpenMV SPI Block Size`.
#define SPI_RECEPTION_RING_BUFFER_LENGTH 32
#define WATCHDOG_DURATION_US             (10 * 60'000'000)
#define MAX_ANGULAR_ACCELERATION         (100.0f)
#define MAX_ANGULAR_VELOCITY             (1000.0f * 2.0f * PI / 60.0f)
#define CONTROLLER_MOTOR_DEMO            false
#define CONTROLLER_MOTOR_ENABLE          true
#define VN100_ENABLE                     true
#define OPENMV_ENABLE                    true
#define ESP32_ENABLE                     true
#define WATCHDOG_ENABLE                  true
#define TRANSMIT_TV                      false

#include "system.h"
#include "timekeeping.c"
#include "uxart.c"
#include "spi.c"
#include "sd.c"
#include "filesystem.c"
#include "stepper.c"
#include "buzzer.c"
#include "i2c.c"
#include "mathematics.c"



////////////////////////////////////////////////////////////////////////////////



pack_push

    struct VN100Packet
    {
        f32 QuatX;
        f32 QuatY;
        f32 QuatZ;
        f32 QuatS;
        f32 MagX;
        f32 MagY;
        f32 MagZ;
        f32 AccelX;
        f32 AccelY;
        f32 AccelZ;
        f32 GyroX;
        f32 GyroY;
        f32 GyroZ;
    };

    struct OpenMVPacket // @/`OpenMV Packet Format`: Coupled.
    {
        union
        {

            // @/`OpenMV Sequence Number`:
            // First image chunk begins at `1`; zero is reserved for `OpenMVPacketGNC`.

            u16 sequence_number;

            struct OpenMVPacketGNC
            {
                u16 zero;
                f32 attitude_yaw;
                f32 attitude_pitch;
                f32 attitude_roll;
                u16 computer_vision_processing_time_ms;
                u8  computer_vision_confidence;
                u8  padding[47];
            } gnc;

            struct OpenMVPacketImage
            {
                u16 sequence_number;
                u8  bytes[62];
            } image;

        };
    };

    static_assert(sizeof(struct OpenMVPacketGNC  ) == sizeof(struct OpenMVPacket));
    static_assert(sizeof(struct OpenMVPacketImage) == sizeof(struct OpenMVPacket));

pack_pop

enum OpenMVImageState : u32
{
    OpenMVImageState_empty,
    OpenMVImageState_filling,
    OpenMVImageState_filled,
    OpenMVImageState_using,
};

struct OpenMVImage
{
    volatile _Atomic enum OpenMVImageState state;
    u8                                     bytes[16 * 1024]; // Average worst ~8 KiB when using YUV422, SIF, 50% quality.
    i32                                    size;
};

struct GNCInfo
{
    struct VN100Packet vn100_packet;
    f32                attitude_yaw;
    f32                attitude_pitch;
    f32                attitude_roll;
};

static struct
{
    RingBuffer(struct VN100Packet    , 8) vn100_packets;
    RingBuffer(struct OpenMVPacketGNC, 8) openmv_gnc_packets;
    volatile struct StepperTuple          current_angular_accelerations;
    volatile struct StepperTuple          current_angular_velocities;
} CONTROLLER = {0};

static struct
{
    RingBuffer(struct VN100Packet    , 8) vn100_packets;
    RingBuffer(struct OpenMVPacketGNC, 8) openmv_gnc_packets;
    volatile _Atomic i32                  stepper_issues;
    volatile _Atomic i32                  vn100_issues;
    volatile _Atomic i32                  openmv_issues;
    volatile _Atomic i32                  esp32_issues;
} LOGGER = {0};

static struct
{
    volatile _Atomic b32 magnetic_disturbance_exists;
    volatile _Atomic b32 acceleration_disturbance_exists;
} VN100 = {0};

static struct
{
    RingBuffer(struct GNCInfo, 8) gnc_infos;
    struct OpenMVImage            openmv_image;
} ESP32 = {0};

static struct
{
    volatile _Atomic u32 most_recent_transfer_timestamp_us;
} VEHICLE_INTERFACE = {0};



////////////////////////////////////////////////////////////////////////////////



extern noret void
main(void)
{

    // General peripheral initializations.

    STPY_init();
    UXART_reinit(UXARTHandle_stlink);



    // Set the prescaler that'll affect all timers' kernel frequency.

    CMSIS_SET(RCC, CFGR1, TIMPRE, STPY_GLOBAL_TIMER_PRESCALER);



    // Configure the other registers to get timekeeping up and going.

    TIMEKEEPING_partial_init();



    // When the vehicle becomes powered on, it's typically because
    // of the external power supply through the vehicle interface.
    // To make sure that the vehicle should stay powered on with
    // the battery supply, we play a tune that'll act as the delay.

    BUZZER_partial_init();

    BUZZER_play(BuzzerTune_waking_up);

    while (BUZZER_current_tune());

    GPIO_ACTIVE(battery_allowed);



    // Set up direct communication with main.

    I2C_partial_reinit(I2CHandle_vehicle_interface);



    // Begin the FreeRTOS task scheduler.

    FREERTOS_init();

}



////////////////////////////////////////////////////////////////////////////////



enum DiagnosticLEDBehavior : u32
{
    DiagnosticLEDBehavior_inactive,
    DiagnosticLEDBehavior_active,
    DiagnosticLEDBehavior_toggle,
};

#include "VehicleFlightComputer_diagnostics.meta"
/* #meta

    DIAGNOSTICS = ( # Ordered from highest priority to lowest priority.
        ('stepper_driver_issue'      , 'ambulance' , ('toggle'  , 'inactive', 'inactive'),  25),
        ('angular_velocity_saturated', 'heartbeat' , ('toggle'  , 'inactive', 'inactive'), 500),
        ('wiping_filesystem'         , 'tetris'    , ('toggle'  , 'inactive', 'toggle'  ), 100),
        ('esp32_mishap'              , 'mario'     , ('toggle'  , 'toggle'  , 'toggle'  ),  25),
        ('openmv_mishap'             , 'three_tone', ('toggle'  , 'toggle'  , 'toggle'  ),  25),
        ('vn100_mishap'              , 'hazard'    , ('inactive', 'inactive', 'toggle'  ),  25),
        ('redocked'                  , 'nokia'     , ('toggle'  , 'toggle'  , 'toggle'  ), 250),
        ('ejection'                  , 'birthday'  , ('toggle'  , 'toggle'  , 'toggle'  ), 500),
        ('logging_mishap'            , 'heavy_beep', ('toggle'  , 'inactive', 'toggle'  ), 100),
        ('vn100_heartbeat'           , 'burp'      , ('inactive', 'inactive', 'active'  ), 100),
        ('logging_heartbeat'         , 'chirp'     , ('inactive', 'active'  , 'inactive'), 100),
    )

    Meta.enums('DiagnosticMask', 'u32', (
        (name, f'1 << {diagnostic_i}')
        for diagnostic_i, (name, tune, (behavior_red, behavior_green, behavior_blue), delay_ms) in enumerate(DIAGNOSTICS)
    ))

    Meta.lut('DIAGNOSTIC_TABLE', ((
        (
            ('tune'          , f'BuzzerTune_{tune}'                     ),
            ('behavior_red'  , f'DiagnosticLEDBehavior_{behavior_red  }'),
            ('behavior_green', f'DiagnosticLEDBehavior_{behavior_green}'),
            ('behavior_blue' , f'DiagnosticLEDBehavior_{behavior_blue }'),
            ('delay_ms'      , f'{delay_ms}U'                           ),
        )
        for diagnostic_i, (name, tune, (behavior_red, behavior_green, behavior_blue), delay_ms) in enumerate(DIAGNOSTICS)
    )))

*/

FREERTOS_TASK(diagnostics, 2)
{

    u32 current_flags = 0;

    for (;;)
    {



        // Check and wait for there to be a new diagnostic to handle.

        b32 waiting = false;

        do
        {

            u32 new_flags = {0};

            BaseType_t got_notification =
                xTaskNotifyWait
                (
                    0,
                    (u32) -1, // Immediately acknowledge the new diagnostics.
                    (uint32_t*) &new_flags,
                    waiting ? 100 : 0
                );

            if (got_notification)
            {
                current_flags |= new_flags;
            }

            waiting = true;

        }
        while (!current_flags);



        // Handle the highest priority diagnostic with buzzer tunes and blinking LEDs.

        enum DiagnosticMask current_diagnostic = current_flags & -current_flags;

        GPIO_INACTIVE(led_channel_red  );
        GPIO_INACTIVE(led_channel_green);
        GPIO_INACTIVE(led_channel_blue );

        if (current_diagnostic && __builtin_ctz(current_diagnostic) < countof(DIAGNOSTIC_TABLE))
        {

            auto info = &DIAGNOSTIC_TABLE[__builtin_ctz(current_diagnostic)];

            BUZZER_play(info->tune);

            while (BUZZER_current_tune())
            {



                // Control the LEDs.

                switch (info->behavior_red)
                {
                    case DiagnosticLEDBehavior_inactive : GPIO_INACTIVE(led_channel_red); break;
                    case DiagnosticLEDBehavior_active   : GPIO_ACTIVE  (led_channel_red); break;
                    case DiagnosticLEDBehavior_toggle   : GPIO_TOGGLE  (led_channel_red); break;
                    default                             : sus;
                }

                switch (info->behavior_green)
                {
                    case DiagnosticLEDBehavior_inactive : GPIO_INACTIVE(led_channel_green); break;
                    case DiagnosticLEDBehavior_active   : GPIO_ACTIVE  (led_channel_green); break;
                    case DiagnosticLEDBehavior_toggle   : GPIO_TOGGLE  (led_channel_green); break;
                    default                             : sus;
                }

                switch (info->behavior_blue)
                {
                    case DiagnosticLEDBehavior_inactive : GPIO_INACTIVE(led_channel_blue); break;
                    case DiagnosticLEDBehavior_active   : GPIO_ACTIVE  (led_channel_blue); break;
                    case DiagnosticLEDBehavior_toggle   : GPIO_TOGGLE  (led_channel_blue); break;
                    default                             : sus;
                }



                // See if there's a new higher priority diagnostic we should handle.

                u32 new_flags = 0;

                BaseType_t got_notification =
                    xTaskNotifyWait
                    (
                        0,
                        (u32) -1, // Immediately acknowledge the new diagnostics.
                        (uint32_t*) &new_flags,
                        0
                    );

                if (got_notification)
                {
                    current_flags |= new_flags; // Add the new diagnostics to the list of existing ones to process.
                }

                enum DiagnosticMask new_diagnostic = current_flags & -current_flags;

                if (new_diagnostic == current_diagnostic)
                {

                    // Although `xTaskNotifyWait` has a time-out argument that could be used
                    // as a delay that can also be interrupted early when there's a notification,
                    // it's possible that a task set the same diagnostic repeatedly over and
                    // over again to which a delay never really happens. By using a regular
                    // task delay here, we're making things slightly less responsive because
                    // the delay won't allow for the `diagnostics` task to handle a new
                    // diagnostic of higher priority, but since this is literally just for
                    // diagnostics, it's okay.

                    FREERTOS_delay_ms(info->delay_ms);

                }
                else
                {
                    break; // There's a new diagnostic of higher priority that we should handle.
                }

            }

        }
        else
        {
            sus; // Invalid diagnostic..?
        }

        GPIO_INACTIVE(led_channel_red  );
        GPIO_INACTIVE(led_channel_green);
        GPIO_INACTIVE(led_channel_blue );

        current_flags &= ~current_diagnostic; // Acknowledge the completion of the diagnostic.

    }

}



////////////////////////////////////////////////////////////////////////////////



volatile _Atomic b32 vehicle_undocked              = false;
volatile         u32 vehicle_ejection_timestamp_us = {0};

FREERTOS_TASK(watchdog, 4)
{

#if WATCHDOG_ENABLE

    b32 noticed_vehicle_interface_pulled_down      = false;
    u32 vehicle_interface_pulled_down_timestamp_us = {0};
    u32 same_dock_state_timestamp_us               = {0};

    for (;;)
    {



        // We need to ensure the vehicle doesn't stay on for long when it's still
        // docked in the ejection mechanism. This is especially important during sequence
        // testing when the vehicle might be powered on but no ejection will take place.
        //
        // We can tell when we have ejected if we're no longer detecting external
        // power, haven't received I2C transfers through the vehicle interface in a while,
        // and that the I2C bus lines are held high by the on-board's pull-up resistors.
        //
        // However, if we're still docked, then the I2C bus lines will actually be pulled
        // low because main is no longer powered, and the on-board's pull-up resistors are
        // weak enough that the MCU doesn't register this as an active level. In this
        // scenario, we should do a reset also.

        u32 observed_most_recent_transfer_timestamp_us =
            atomic_load_explicit
            (
                &VEHICLE_INTERFACE.most_recent_transfer_timestamp_us,
                memory_order_relaxed // No synchronization needed.
            );

        b32 theres_still_external_power             = GPIO_READ(external_detected);
        b32 vehicle_interface_currently_pulled_down = !GPIO_READ(vehicle_interface_i2c_clock) && !GPIO_READ(vehicle_interface_i2c_data);

        if (!vehicle_interface_currently_pulled_down)
        {
            noticed_vehicle_interface_pulled_down = false;
        }
        else if (!noticed_vehicle_interface_pulled_down)
        {
            noticed_vehicle_interface_pulled_down      = true;
            vehicle_interface_pulled_down_timestamp_us = TIMEKEEPING_microseconds();
        }

        b32 docked_reset =
            (
                !theres_still_external_power &&
                vehicle_interface_currently_pulled_down &&
                TIMEKEEPING_microseconds() - vehicle_interface_pulled_down_timestamp_us >= 10'000'000 &&
                TIMEKEEPING_microseconds() - observed_most_recent_transfer_timestamp_us >= 10'000'000
            );

        if (docked_reset)
        {

            // Indicate that this is why the vehicle is suddenly shut off.

            BUZZER_play(BuzzerTune_starwars);
            while (BUZZER_current_tune());



            // Try cut off battery power.

            GPIO_INACTIVE(battery_allowed);
            spinlock_us(1'000'000);



            // If we're still alive by this point, then
            // there's probably external power or something,
            // to which we'll just do a software reset.

            WARM_RESET();

        }



        // See if the vehicle's dock status has changed.

        b32 observed_vehicle_undocked =
            atomic_load_explicit
            (
                &vehicle_undocked,
                memory_order_relaxed // No synchronization needed.
            );

        b32 currently_undocked =
            (
                !theres_still_external_power &&
                !vehicle_interface_currently_pulled_down &&
                TIMEKEEPING_microseconds() - observed_most_recent_transfer_timestamp_us >= 1'000'000
            );

        if (!!currently_undocked == !!observed_vehicle_undocked)
        {
            same_dock_state_timestamp_us = TIMEKEEPING_microseconds();
        }

        if (TIMEKEEPING_microseconds() - same_dock_state_timestamp_us >= 5'000'000)
        {

            if (currently_undocked) // We just ejected!
            {

                vehicle_ejection_timestamp_us = TIMEKEEPING_microseconds();

                atomic_store_explicit
                (
                    &vehicle_undocked,
                    currently_undocked,
                    memory_order_release // We updated the ejection timestamp.
                );


                xTaskNotify
                (
                    diagnostics_handle,
                    DiagnosticMask_ejection,
                    eSetBits
                );

            }
            else // We got reinserted into the ejection mechanism...
            {

                atomic_store_explicit
                (
                    &vehicle_undocked,
                    currently_undocked,
                    memory_order_relaxed // No synchronization necessary.
                );

                xTaskNotify
                (
                    diagnostics_handle,
                    DiagnosticMask_redocked,
                    eSetBits
                );
            }

        }



        FREERTOS_delay_ms(1'000);

    }

#else

    for (;;)
    {
        FREERTOS_delay_ms(1'000);
    }

#endif

}



////////////////////////////////////////////////////////////////////////////////
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

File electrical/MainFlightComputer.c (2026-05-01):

#define WATCHDOG_ENABLE                  true
#define ALLOW_FILESYSTEM_TO_BE_FORMATTED false
#define TRANSMIT_TV                      false
#define SOLARBOARD_ANALOG_FACTOR         (1.0f / 620.0f)

#include "system.h"
#include "timekeeping.c"
#include "uxart.c"
#include "i2c.c"
#include "sd.c"
#include "filesystem.c"



////////////////////////////////////////////////////////////////////////////////



extern noret void
main(void)
{

    // General peripheral initializations.

    STPY_init();
    UXART_reinit(UXARTHandle_stlink);



    // Set the prescaler that'll affect all timers' kernel frequency.

    CMSIS_SET(RCC, CFGR1, TIMPRE, STPY_GLOBAL_TIMER_PRESCALER);



    // Configure the other registers to get timekeeping up and going.

    TIMEKEEPING_partial_init();



    // Indicate we are alive and well.

    for (i32 i = 0; i < 8; i += 1)
    {

        GPIO_ACTIVE  (led_channel_red  );
        GPIO_INACTIVE(led_channel_green);
        GPIO_INACTIVE(led_channel_blue );
        spinlock_us(20'000);

        GPIO_ACTIVE  (led_channel_red  );
        GPIO_ACTIVE  (led_channel_green);
        GPIO_INACTIVE(led_channel_blue );
        spinlock_us(20'000);

        GPIO_INACTIVE(led_channel_red  );
        GPIO_ACTIVE  (led_channel_green);
        GPIO_INACTIVE(led_channel_blue );
        spinlock_us(20'000);

        GPIO_INACTIVE(led_channel_red  );
        GPIO_ACTIVE  (led_channel_green);
        GPIO_ACTIVE  (led_channel_blue );
        spinlock_us(20'000);

        GPIO_INACTIVE(led_channel_red  );
        GPIO_INACTIVE(led_channel_green);
        GPIO_ACTIVE  (led_channel_blue );
        spinlock_us(20'000);

        GPIO_ACTIVE  (led_channel_red  );
        GPIO_INACTIVE(led_channel_green);
        GPIO_ACTIVE  (led_channel_blue );
        spinlock_us(20'000);

    }

    GPIO_INACTIVE(led_channel_red  );
    GPIO_INACTIVE(led_channel_green);
    GPIO_INACTIVE(led_channel_blue );



    // Begin the FreeRTOS task scheduler.

    FREERTOS_init();

}



////////////////////////////////////////////////////////////////////////////////



enum DiagnosticLEDBehavior : u32
{
    DiagnosticLEDBehavior_inactive,
    DiagnosticLEDBehavior_active,
    DiagnosticLEDBehavior_toggle,
};

#include "MainFlightComputer_diagnostics.meta"
/* #meta

    DIAGNOSTICS = ( # Ordered from highest priority to lowest priority.
        ('watchdog_reset'          , ('toggle'  , 'inactive', 'inactive'), 200, 3000),
        ('wiping_filesystem'       , ('toggle'  , 'toggle'  , 'toggle'  ),  25, 4000),
        ('logging_mishap'          , ('toggle'  , 'inactive', 'toggle'  ),  25,  250),
        ('esp32_mishap'            , ('inactive', 'inactive', 'toggle'  ),  50,  500),
        ('vehicle_interface_mishap', ('toggle'  , 'toggle'  , 'toggle'  ),  25,  250),
        ('logging_heartbeat'       , ('inactive', 'active'  , 'inactive'),  25,   25),
    )

    Meta.enums('DiagnosticMask', 'u32', (
        (name, f'1 << {diagnostic_i}')
        for diagnostic_i, (name, (behavior_red, behavior_green, behavior_blue), delay_ms, duration_ms) in enumerate(DIAGNOSTICS)
    ))

    Meta.lut('DIAGNOSTIC_TABLE', ((
        (
            ('behavior_red'  , f'DiagnosticLEDBehavior_{behavior_red  }'),
            ('behavior_green', f'DiagnosticLEDBehavior_{behavior_green}'),
            ('behavior_blue' , f'DiagnosticLEDBehavior_{behavior_blue }'),
            ('delay_ms'      , f'{delay_ms}U'                           ),
            ('duration_ms'   , f'{duration_ms}U'                        ),
        )
        for diagnostic_i, (name, (behavior_red, behavior_green, behavior_blue), delay_ms, duration_ms) in enumerate(DIAGNOSTICS)
    )))

*/

FREERTOS_TASK(diagnostics, 1)
{

    u32 current_flags = 0;

    for (;;)
    {



        // Check and wait for there to be a new diagnostic to handle.

        b32 waiting = false;

        do
        {

            u32 new_flags = {0};

            BaseType_t got_notification =
                xTaskNotifyWait
                (
                    0,
                    (u32) -1, // Immediately acknowledge the new diagnostics.
                    (uint32_t*) &new_flags,
                    waiting ? 100 : 0
                );

            if (got_notification)
            {
                current_flags |= new_flags;
            }

            waiting = true;

        }
        while (!current_flags);



        // Handle the highest priority diagnostic with blinking LEDs.

        enum DiagnosticMask current_diagnostic = current_flags & -current_flags;

        GPIO_INACTIVE(led_channel_red  );
        GPIO_INACTIVE(led_channel_green);
        GPIO_INACTIVE(led_channel_blue );

        if (current_diagnostic && __builtin_ctz(current_diagnostic) < countof(DIAGNOSTIC_TABLE))
        {

            auto info = &DIAGNOSTIC_TABLE[__builtin_ctz(current_diagnostic)];

            u32 start_timestamp_us = TIMEKEEPING_microseconds();

            while (TIMEKEEPING_microseconds() - start_timestamp_us < info->duration_ms * 1000)
            {



                // Control the LEDs.

                switch (info->behavior_red)
                {
                    case DiagnosticLEDBehavior_inactive : GPIO_INACTIVE(led_channel_red); break;
                    case DiagnosticLEDBehavior_active   : GPIO_ACTIVE  (led_channel_red); break;
                    case DiagnosticLEDBehavior_toggle   : GPIO_TOGGLE  (led_channel_red); break;
                    default                             : sus;
                }

                switch (info->behavior_green)
                {
                    case DiagnosticLEDBehavior_inactive : GPIO_INACTIVE(led_channel_green); break;
                    case DiagnosticLEDBehavior_active   : GPIO_ACTIVE  (led_channel_green); break;
                    case DiagnosticLEDBehavior_toggle   : GPIO_TOGGLE  (led_channel_green); break;
                    default                             : sus;
                }

                switch (info->behavior_blue)
                {
                    case DiagnosticLEDBehavior_inactive : GPIO_INACTIVE(led_channel_blue); break;
                    case DiagnosticLEDBehavior_active   : GPIO_ACTIVE  (led_channel_blue); break;
                    case DiagnosticLEDBehavior_toggle   : GPIO_TOGGLE  (led_channel_blue); break;
                    default                             : sus;
                }



                // See if there's a new higher priority diagnostic we should handle.

                u32 new_flags = 0;

                BaseType_t got_notification =
                    xTaskNotifyWait
                    (
                        0,
                        (u32) -1, // Immediately acknowledge the new diagnostics.
                        (uint32_t*) &new_flags,
                        0
                    );
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

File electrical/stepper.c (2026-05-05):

#ifndef STEPPER_ENABLE_DELAY_US
#error "Please define `STEPPER_ENABLE_DELAY_US`! See @/`Stepper Enable Delay`."
#endif

#ifndef STEPPER_VELOCITY_UPDATE_US
#error "Please define `STEPPER_VELOCITY_UPDATE_US`! See @/`Stepper Updating Velocity`."
#endif

#ifndef STEPPER_UART_TIME_MARGIN_US
#error "Please define `STEPPER_UART_TIME_MARGIN_US`! See @/`Stepper UART Time Margin Window`."
#endif

#ifndef STEPPER_RING_BUFFER_LENGTH
#error "Please define `STEPPER_RING_BUFFER_LENGTH`! See @/`Stepper Ring-Buffer Length`."
#endif

enum StepperMicrostepResolution : u32 // @/pg 33/tbl 5.5.1/`TMC2209`.
{
    StepperMicrostepResolution_256 = 0b0000,
    StepperMicrostepResolution_128 = 0b0001,
    StepperMicrostepResolution_64  = 0b0010,
    StepperMicrostepResolution_32  = 0b0011,
    StepperMicrostepResolution_16  = 0b0100,
    StepperMicrostepResolution_8   = 0b0101,
    StepperMicrostepResolution_4   = 0b0110,
    StepperMicrostepResolution_2   = 0b0111,
    StepperMicrostepResolution_1   = 0b1000,
};

// @/`Stepper Microstepping and Step Velocity`.
#define STEPPER_MICROSTEP_RESOLUTION StepperMicrostepResolution_16
#define STEPPER_STEPS_PER_REVOLUTION ((f32) (((1 << (8 - STEPPER_MICROSTEP_RESOLUTION)) * 200) / 0.715f))

static const struct StepperInitializationSequenceEntry { u8 register_address; u32 data; } STEPPER_INITIALIZATION_SEQUENCE[] =
    {
        {
            0x00,      // "GCONF"            : @/pg 23/tbl 5.1/`TMC2209`.
              (1 << 0) // "I_scale_analog"   : Whether or not to use VREF as current reference.
            | (1 << 2) // "en_SpreadCycle"   : Whether or not to only use SpreadCycle (louder and more power, but more torque); otherwise, a mix of StealthChop and SpreadCycle is done.
            | (1 << 6) // "pdn_disable"      : The power-down and UART functionality both share the same pin, so we disable the former.
            | (1 << 7) // "mstep_reg_select" : Microstep resolution determined by a register field rather than the MS1/MS2 pins.
        },
        {
            0x03,    // "NODECONF"  : @/pg 24/tbl 5.1/`TMC2209`.
            (3 << 8) // "SENDDELAY" : Amount of delay before the read response is sent back.
        },
        {
            0x10,            // "IHOLD_IRUN" : @/pg 28/tbl 5.2/`TMC2209`.
              ((1 - 1) << 0) // "IHOLD"      : Standstill current (out of 32) for when the motor is not turning.
            | ((3 - 1) << 8) // "IRUN"       : Current scaling (out of 32) for when the motor is turning.
        },
        {
            0x6C,                                  // "CHOPCONF" : @/pg 33/tbl 5.5.1/`TMC2209`.
              (0                            << 31) // "diss2vs"  : "0: Short protection low side is on".
            | (0                            << 30) // "diss2g"   : "0: Short to GND protection is on".
            | (0                            << 28) // "intpol"   : The actual microstep resolution is "extrapolated to 256 microsteps for smoothest motor operation".
            | (STEPPER_MICROSTEP_RESOLUTION << 24) // "MRES"     : Microstep resolution.
            | (5                            <<  4) // "HSTRT"    : Addend to "hysteresis low value HEND".
            | (3                            <<  0) // "TOFF"     : "Off time setting controls duration of slow decay phase".
        },
    };

#include "stepper_driver_support.meta"
/* #meta

    for target in PER_TARGET():

        # Ensure there's a unique stepper driver.

        driver = [
            driver
            for driver in target.drivers
            if driver['type'] == 'Stepper'
        ]

        if len(driver) != 1:
            Meta.line(f'#error Target {repr(target.name)} needs to define a unique {repr('Stepper')} driver.')
            continue

        driver, = driver



        # Supporting definitions.

        Meta.enums('StepperUnit', 'u32', (
            name
            for name, address in driver['units']
        ))

        Meta.lut('STEPPER_INSTANCE_TABLE', ((
            ('u8', 'address', address),
        ) for name, address in driver['units']))

        # TODO Inconvenient:
        Meta.define('STEPPER_UXART_HANDLE'                   , f'UXARTHandle_{driver['uxart_handle']}')
        Meta.define('STEPPER_MOTOR_ENABLE'                   , driver['enable_gpio'])
        Meta.define('STEPPER_TIMx'                           ,                         f'{driver['timer_peripheral']}'           )
        Meta.define('STEPPER_TIMx_'                          ,                         f'{driver['timer_peripheral']}_'          )
        Meta.define('STEPPER_TIMx_RESET'                     , CMSIS_TUPLE(target.mcu, f'{driver['timer_peripheral']}_RESET' )   )
        Meta.define('STEPPER_TIMx_ENABLE'                    , CMSIS_TUPLE(target.mcu, f'{driver['timer_peripheral']}_ENABLE')   )
        Meta.define('STEPPER_STPY_TIMx_DIVIDER'              ,                    f'STPY_{driver['timer_peripheral']}_DIVIDER'   )
        Meta.define('STEPPER_STPY_TIMx_MODULATION'           ,                    f'STPY_{driver['timer_peripheral']}_MODULATION')
        Meta.define('NVICInterrupt_STEPPER_TIMx_update_event',          f'NVICInterrupt_{driver['timer_update_event_interrupt']}')
        Meta.define('INTERRUPT_STEPPER_TIMx_update_event'    ,              f'INTERRUPT_{driver['timer_update_event_interrupt']}')
        Meta.define('STEPPER_UPDATE_EVENT_PERIOD_US'         , round(1_000_000 / target.schema[f'{driver['timer_peripheral']}_UPDATE_RATE']))

*/

#define STEPPER_TMC2209_IFCNT_ADDRESS   0x02 // @/pg 24/tbl 5.1/`TMC2209`.
#define STEPPER_TMC2209_VACTUAL_ADDRESS 0x22 // @/pg 28/tbl 5.2/`TMC2209`.

static_assert(STEPPER_ENABLE_DELAY_US     % STEPPER_UPDATE_EVENT_PERIOD_US == 0);
static_assert(STEPPER_VELOCITY_UPDATE_US  % STEPPER_UPDATE_EVENT_PERIOD_US == 0);
static_assert(STEPPER_UART_TIME_MARGIN_US % STEPPER_UPDATE_EVENT_PERIOD_US == 0);

struct StepperTuple
{
    f32 values[StepperUnit_COUNT];
};

enum StepperUARTState : u32
{
    StepperUARTState_standby,
    StepperUARTState_read_scheduled,
    StepperUARTState_read_requested,
    StepperUARTState_write_scheduled,
    StepperUARTState_write_verification_read_scheduled,
    StepperUARTState_write_verification_read_requested,
    StepperUARTState_done,
};

enum StepperDriverState : u32
{
    StepperDriverState_disabled,
    StepperDriverState_initializing_uart_write_sequence_numbers,
    StepperDriverState_doing_initialization_sequences,
    StepperDriverState_delaying_enable,
    StepperDriverState_waiting_on_angular_velocities,
    StepperDriverState_updating_angular_velocities,
    StepperDriverState_no_response_from_unit,
    StepperDriverState_bad_response_from_unit,
};
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

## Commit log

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2025-10-19 Added footprints for TMC2209, PDS housing, and edge-cuts.
    [35WR10KLFTR.step, PowerDistributionSystem.kicad_pcb, PowerDistributionSystem.kicad_sch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]
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2025-10-20 CONSat model in the PCB model folder to fix the relative path.
    [PowerDistributionSystem.kicad_pcb]
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2025-10-21 Accounting for burn-wire connector.
    [PowerDistributionSystem.kicad_sch]
2025-10-21 Reworked TMC2209 so that the three drivers have things in common (e.g. enable/disable pin).
    [PowerDistributionSystem.kicad_pcb, PowerDistributionSystem.kicad_sch, PowerDistributionSystem_Stepper_Motor_Driver_TMC2209.kicad_sch]
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2025-10-21 Actually fixed the relative path.
    [PowerDistributionSystem.kicad_pcb]
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2025-10-24 Added visualization for other stacks in the main stack-up.
    [ElectronicsBoxCase_AN-14F-01_Body.step, ElectronicsBoxCase_AN-14F-01_Lid.step, MainFlightComputer.kicad_pcb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]
2025-10-24 Adjusted dimensions to potentially support stack-up of 4 PCBs.
    [MainFlightComputer.kicad_pcb, Main_Stack_Dummy.step]
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2025-10-24 Fixed footprint of TMC2209-LA-T.
    [PowerDistributionSystem.kicad_pcb, PowerDistributionSystem_Stepper_Motor_Driver_TMC2209.kicad_sch]
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2025-10-24 Moved the main stack pin-outs into a hierarchical sheet.
    [MainFlightComputer.kicad_pcb, MainFlightComputer.kicad_sch, MainFlightComputer_Main_Stack_Pin_Outs.kicad_sch]
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2025-10-27 Made the stack edge-cuts, pin-outs, and mounting holes be part of a symbol and footprint.
    [MainFlightComputer.kicad_pcb, MainFlightComputer.kicad_sch, MainFlightComputer_Main_Stack_Pin_Outs.kicad_sch]
2025-10-27 Power distribution board using the PCB stack-up symbol.
    [PowerDistributionSystem.kicad_pcb, PowerDistributionSystem.kicad_sch]
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2025-10-29 Revert "Model for 66-pin Amphenol Receptacle"
    [tv07rw23-35p.SLDPRT]
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2025-10-29 Fixed pin numbers of S12B-PADSS-1.
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2025-11-04 Revert "New enclosure with connector"
2025-11-04 Instead of S04B-PASK-2 connectors, regular 2.54mm horizontal pin headers will be used.
    [PowerDistributionSystem.kicad_pcb, PowerDistributionSystem.kicad_sch]
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2025-11-05 Added regulators for burn-wire.
    [PowerDistributionSystem.kicad_pcb, PowerDistributionSystem.kicad_sch, PowerDistributionSystem_Burnwire_Regulator.kicad_sch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]
2025-11-05 Routed L4978 burn-wire regulators.
    [PowerDistributionSystem.kicad_pcb, PowerDistributionSystem.kicad_sch, PowerDistributionSystem_Burnwire_Regulator.kicad_sch]
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2025-11-06 `Debug Buzzer (V4 : Transistor).` : Buzzer driven by transistor.
    [Debug_Buzzer.kicad_sch, MainFlightComputer.kicad_sch]
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2025-11-06 `Reset Mechanism (V4 : Removed local-net).`
    [MainFlightComputer.kicad_sch, Reset_Mechanism.kicad_sch]
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2025-11-07 Updated symbol and footprint of the XIAO ESP32 to account for the under pads.
    [MainMiscellaneousBoard.kicad_pcb, MainMiscellaneousBoard.kicad_sch, VehicleMiscellaneousBoard.kicad_pcb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]
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2025-11-07 Reverting deletion of the dummy virtual housing of `VehiclePowerDistributionSystem`.
    [VehiclePowerDistributionSystem.kicad_pcb]
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2025-11-08 Made stack connector for vehicle and laid out some footprints for `VehicleFlightComputer`.
    [VehicleFlightComputer.kicad_pcb, VehicleFlightComputer.kicad_sch]
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2025-11-08 Added in other PCB stacks for virtual housing of `VehicleFlightComputer` and `VehicleMiscellaneousBoard`.
    [VehicleFlightComputer.kicad_pcb, VehicleMiscellaneousBoard.kicad_pcb, Vehicle_Stack_Dummy.step]
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2025-11-08 Different header options for `VehicleStackConnector` and updating the virtual models of vehicle PCBs.
    [VehicleFlightComputer.kicad_pcb, VehicleMiscellaneousBoard.kicad_pcb]
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2025-11-09 `Debug Buzzer (V5 : AST only).`
    [Debug_Buzzer.kicad_sch, VehicleFlightComputer.kicad_sch]
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2025-11-10 Placed footprints and routed USB-UART bridge and reset mechanism for `VehicleFlightComputer`.
    [VehicleFlightComputer.kicad_pcb]
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2025-11-11 `Vehicle PDS I/O (V1 : Fixed pin-count).`
    [VehicleFlightComputer.kicad_pcb, VehicleFlightComputer.kicad_sch, VehiclePowerDistributionSystem.kicad_pcb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]
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2025-11-11 Added uSD connector for `VehicleFlightComputer`; added missing solder jumper footprint for LSM6DSV32X.
    [VehicleFlightComputer.kicad_pcb, VehicleFlightComputer.kicad_sch, VehicleFlightComputer_uSD_Connector.kicad_sch]
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2025-11-11 Removed `Vehicle_Stack_Dummy.step` as it's no longer used.
    [Vehicle_Stack_Dummy.step]
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2025-11-14 Addressed DRC issues with `VehiclePowerDistributionSystem`.
    [VehiclePowerDistributionSystem.kicad_pcb]
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2025-11-14 Fixed orientation of `VehiclePowerDistributionSystem` in `VehicleFlightComputer` and `VehicleMiscellaneousBoard` virtual housing.
    [VehicleFlightComputer.kicad_pcb, VehicleMiscellaneousBoard.kicad_pcb]
2025-11-15 Made `VehicleFlightComputer` target and corrected nets for the STM32H533VET6 on `VehicleFlightComputer` PCB.
    [VehicleFlightComputer.kicad_pcb, VehicleFlightComputer.kicad_sch, VehiclePowerDistributionSystem.kicad_pcb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]
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2025-11-15 Fixed issues reported by `checkPCBs` concerning the stack connectors.
    [MainFlightComputer.kicad_sch, MainPowerDistributionSystem.kicad_sch, MainPowerDistributionSystem_Burnwire_Regulator.kicad_sch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]
2025-11-15 Fixed pads of `Seeed_Studio_XIAO_ESP32_S3` footprint.
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2025-11-15 Fixed inconsistency of `VehicleStackConnector` in `VehicleFlightComputer` and `VehicleMiscellaneousBoard`.
    [VehicleFlightComputer.kicad_pcb, VehicleFlightComputer.kicad_sch, VehicleMiscellaneousBoard.kicad_pcb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]
2025-11-15 Fixed buzzer's transistor footprint.
    [VehicleFlightComputer.kicad_pcb, VehicleFlightComputer.kicad_sch]
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2025-12-02 Moved test-pad for UART line of TMC2209s to top layer of `VehiclePowerDistributionSystem` PCB.
    [VehiclePowerDistributionSystem.kicad_pcb]
2025-12-02 Made schematic symbol of vehicle stack connector match up with the footprint.
    [VehicleFlightComputer.kicad_pcb, VehicleFlightComputer.kicad_sch, VehicleMiscellaneousBoard.kicad_pcb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]
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2025-12-05 Updated main stack-up connector design to go from 6 1x17 headers to only 4 1x17 headers.
    [MainFlightComputer.kicad_pcb, MainFlightComputer.kicad_sch, MainMiscellaneousBoard.kicad_pcb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]
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2025-12-05 Added male headers and short female headers to `MainStackConnector` footprint.
    [MainFlightComputer.kicad_pcb, MainMiscellaneousBoard.kicad_pcb, MainPowerDistributionSystem.kicad_pcb]
2025-12-05 Including Wio-SX1262 LoRa module for the XIAO ESP32 in the `Seeed_Studio_XIAO_ESP32_S3` footprint.
    [MainMiscellaneousBoard.kicad_pcb, VehicleMiscellaneousBoard.kicad_pcb, Wio-SX1262_for_XIAO_3D_file.step]
2025-12-05 Fixed `MainMiscellaneousBoard_uSD_Connector.kicad_sch`; removed silkscreen for edge connector of `MainMiscellaneousBoard`.
    [MainMiscellaneousBoard.kicad_pcb, MainMiscellaneousBoard.kicad_sch, MainMiscellaneousBoard_uSD_Connector.kicad_sch]
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2025-12-05 Errata fix `VFC-R1.1` and `VMISC-R1.1`: forgot to account for vehicle interface I2C bus.
    [VehicleFlightComputer.kicad_pcb, VehicleFlightComputer.kicad_sch, VehicleMiscellaneousBoard.kicad_pcb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]
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2025-12-06 Replaced `12401548E4#2A` with `12401598E4#2A` for `USB_UART_Bridge`.
    [MainFlightComputer.kicad_sch, USB_UART_Bridge.kicad_sch]
2025-12-06 Errata fix `VFC-R1.2`: USB-C receptacle 12401548E4#2A is obsolete and is misrouted.
    [VehicleFlightComputer.kicad_pcb, VehicleFlightComputer.kicad_sch]
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2025-12-07 Fixed compiler issue by removing unnecessary files and cleaned up both main and vehicle code(still going over some things)
    [ESP32Main.ino, ESP32Vehicle.ino]
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2025-12-09 Addressed build issues where `root` would be applied twice to a path.
    [cli.py]
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2025-12-09 No longer having a separate script for `checkPCBs`.
    [cli.py]
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2025-12-10 Replaced `DIRECTORY_PATH_OF_OUTPUTS` with `BUILD`.
    [cli.py]
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2025-12-12 Cleaned up files for final submission Added military standard checksum function(uses CRC32) Removed issue of checksumming unnecessary values
    [ESP32Main.ino, ESP32Vehicle.ino]
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2025-12-13 `stpy`: "Fixed bug that occurred when a GPIO has `None` for its pin."
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2025-12-14 Fixed register initialization write transfer procedure.
    [ovcam.c]
2025-12-14 Some log error messages for malformed streams.
    [cli.py]
2025-12-15 Handling stream errors more robustly; preventing from image data becoming arbitrarily large.
    [cli.py]
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2025-12-16 Setting up to have a swapchain.
    [DemoOVCAM.c, Shared.py, ovcam.c]
2025-12-16 Begin capturing the next frame if there's a framebuffer available in the swapchain.
    [DemoOVCAM.c, ovcam.c]
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2025-12-16 Keybinding for flipping through different orientations.
    [cli.py]
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2025-12-17 Fixed bug with drop-down menu button event from PyGame GUI.
    [cli.py]
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2025-12-19 Fixed missing definitions of `MINIMUM_MAJOR` and `MINIMUM_MINOR`.
    [cli.py]
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2025-12-22 Fixed multi-lined C++ styled comment.
    [system.h]
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2025-12-22 Fixed subtle build issue where the wrong CPU was specified.
    [Shared.py]
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2025-12-22 Sequence number no longer being used as the sync start token; it's separate from `struct PacketLoRa` now.
    [ESP32Vehicle.ino, system.h]
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2025-12-23 Added some traps to catch ring-buffer bug...
    [ESP32Vehicle.ino]
2025-12-24 Documentation of known issues.
    [ESP32Vehicle.ino]
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2026-01-11 Typo.
    Fixed typo where a register for stepper driver where the timer register for channel output 1 was only being modified rather than being dependent on the driver configuration; this made a subtle bug where the motor would move when it should be still.
    [stepper.c]
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2026-01-12 Fixed system definition bug when compiling with FreeRTOS.
    [system.h]
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2026-01-13 Slightly shortened output of `I2C_TABLE`.
    [i2c.c]
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2026-01-13 Extended `I2CMasterCallbackEvent` to include errors.
    [i2c.c]
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2026-01-19 Stepper driver will only enable the motor after initialization has completed to prevent current surge upon power-on.
    [Shared.py, stepper.c]
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2026-01-22 Added some tolerance for the stencil supports.
    [VehicleFlightComputer_support.SLDPRT, VehiclePowerDistributionSystem_support.SLDPRT]
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2026-01-24 Revert "Instead of using repetitions for amount of steps within a certain window of time, a step frequency is set that is then periodically updated."
    This reverts commit d633733780149caf109294a8402a4a0c94a2f419.
    [Shared.py, stepper.c]
2026-01-24 Revert "Stepper driver now has step range of -255 to 255."
    This reverts commit 24ce7d228732a52469c6e480b0756e4891defaa8.
    [stepper.c]
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2026-01-24 Stepper driver no longer associated with a specific UXART handle.
    [Shared.py, VehicleFlightComputer.c, stepper.c]
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2026-01-24 `_STEPPER_update` no longer controls the enabling of the motors.
    [Shared.py, VehicleFlightComputer.c, stepper.c]
2026-01-24 Fixed issue where UART transfers were being updated too soon due to it being updated back-to-back.
    [Shared.py, VehicleFlightComputer.c, stepper.c]
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2026-01-24 Reinitializing all TMC2209s in event of some errors.
    [VehicleFlightComputer.c, stepper.c]
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2026-01-25 Developed driver for buzzer to play tunes.
    [Shared.py, VehicleFlightComputer.c, buzzer.c]
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2026-01-25 Added timekeeping and buzzer usage to `VehicleFlightComputer` target.
    [Shared.py, VehicleFlightComputer.c]
2026-01-25 Fixing errata of missing pull-up resistors on `CMD` and `DAT0` lines of uSD connector.
    [MainCameraSystem_uSD_Connector.kicad_sch, uSD_Connector.kicad_sch]
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2026-01-25 Fixeed schematic error where the wrong regulator was used (`+1.8V` instead of `+1.5V`).
    [MainCameraSystem.kicad_sch]
2026-01-25 Made `XF3M_2415_1B` footprint to replace the `FFC2B28-24-G` ribbon connector.
    [FFC2B28-24-G.step, XF3M_2415_1B.stp]
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2026-01-26 Laid out silkscreen and fixed schematic and PCB issues for `MainCameraSystem`.
    [MainCameraSystem.kicad_pcb, MainCameraSystem.kicad_sch, MainCameraSystem_uSD_Connector.kicad_sch]
2026-01-26 Fixed some sign-ness issues and renamed some UXART routines.
    [DemoOVCAM.c, DemoTimekeeping.c, SandboxNucleoBoard.c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]
2026-01-26 Automatically preventing transmitted data being interpreted as incoming data for half-duplex UXARTs.
    [SandboxNucleoBoard.c, Shared.py]
2026-01-26 Fixed edge-case of half-duplex UXART where receiver wasn't disabled before the transmission.
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2026-01-27 Added burn wire timer to schematic and routed PCB
    [MainPowerDistributionSystem.kicad_pcb, MainPowerDistributionSystem.kicad_sch]
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2026-01-27 Changes, mainly reducing tolerance for shaft.
    [MockPrint.SLDPRT]
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2026-01-27 Debug buzzer simplified.
    [DebugBoard.kicad_sch, Debug_Buzzer.kicad_sch]
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2026-01-28 Made `DebugBoard` target and fixed some GPIO discrepancies.
    [DebugBoard.kicad_sch, DebugBoard_Button.kicad_sch, DebugBoard_RGB_LED.kicad_sch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]
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2026-01-30 Using `VMISC` to have `VehicleFlightComputer` transmit data to vehicle ESP32 (also adapting to errata where ESP32 transfer will be using UART instead of SPI).
    [Shared.py, VehicleFlightComputer.c]
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2026-01-30 Addressed ERC schematic issues for `VehicleFlightComputer`.
    [VehicleFlightComputer.kicad_sch, VehicleFlightComputer_uSD_Connector.kicad_sch, Vehicle_PDS_IO.kicad_sch]
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2026-02-01 Fixed burn-wire enable circuit on schematic and PCB for MPDS
    [MainPowerDistributionSystem.kicad_pcb, MainPowerDistributionSystem.kicad_sch]
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2026-02-05 Extended `IMPLEMENT_DRIVER_SUPPORT` to have `expansions` parameter; simplified SPI driver by no longer having useless `_SPI_drivers`.
    [i2c.c, spi.c, system.h]
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2026-02-06 Addressing CRC issue with OpenMV.
    [Shared.py]
2026-02-06 SPI driver detecting CRC errors.
    [spi.c]
2026-02-06 SPI transfers in terms of fixed-size blocks.
    [VehicleFlightComputer.c, spi.c]
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2026-02-06 Using ring-buffer for swapchain.
    [DemoOVCAM.c, ovcam.c]
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2026-02-07 I2C driver now detects when clock-stretching goes on for too long.
    [DemoI2C.c, MainFlightComputer.c, Shared.py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]
2026-02-07 No longer using escaping backslashes as it does not work with Windows' CMD shell.
    [Shared.py]
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2026-02-08 Fixed really bad off-by-one error with DMA repetition count.
    [ovcam.c]
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2026-02-08 Having `DemoOVCAM` reinitialize the OVCAM driver upon a crash.
    [DemoOVCAM.c, ovcam.c]
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2026-02-11 Shutting down by peripheral with the RCC reset registers by only setting them to true without a full true/false cycle.
    [i2c.c, ovcam.c]
2026-02-12 Added another error condition for ST-Links returned by `STM32_Programmer_CLI`.
    [cli.py]
2026-02-15 Made `bug` macro to make it easy to halt on bug conditions.
    [i2c.c, system.h]
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2026-02-20 Fixed bug where SD driver would get in perpetual loop due to incorrect logic for determining the value of `stop_requesting_for_data_blocks`.
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2026-02-22 Using the `bug` macro for `ovcam.c`.
    [ovcam.c]
2026-02-22 Replaced `volatile` with `_Atomic` for OVCAM driver.
    [ovcam.c]
2026-02-22 Deprecated `panic` and documented how error-handling should be done.
    [DemoI2C.c, DemoOVCAM.c, DemoSDMMC.c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]
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2026-02-23 `DemoSDMMC` target reinitializing file-system driver after error.
    [DemoSDMMC.c]
2026-02-24 Made error code `FileSystemReinitResult_no_more_space_for_new_file`.
    [DemoSDMMC.c]
2026-02-24 Renamed `missing_filesystem` error to `invalid_filesystem`.
    [DemoSDMMC.c]
2026-02-24 Made `OVCAMSwapFramebufferResult_timeout` error condition.
    [DemoOVCAM.c, ovcam.c]
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2026-02-24 Minor clean up of I2C driver update routine; fixed bug where I2C driver's master state would be set, even for slave mode.
    [i2c.c]
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2026-02-25 Better handling of misbehaving bus error conditions; better handling of repeated START conditions.
    [DemoI2C.c, MainFlightComputer.c, VehicleFlightComputer.c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]
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2026-02-25 Added missing callbacks triggers for repeated START conditions.
    [i2c.c]
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2026-02-25 Marking unexpected `I2CInterruptEvent_clock_stretch_timeout` as `bus_misbehaved` instead of `bug`.
    [i2c.c]
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2026-02-26 Reinitializing even with I2C error for `DemoOVCAM` target.
    [DemoOVCAM.c]
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2026-02-26 Clarifying error handling for the SPI driver.
    [spi.c]
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2026-02-27 Using `Meta.lut` for `BUZZER_TUNES`.
    [buzzer.c]
2026-02-27 Cleaned up buzzer driver.
    [Shared.py, VehicleFlightComputer.c, buzzer.c]
2026-02-27 Having a CSV file of mock GNC input data to simulate from.
    [GNC_MOCK_SIMULATION.csv]
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2026-02-28 Revert "Added FSPI for LoRa RadioLib initialization and documented LoRa parameters."
    This reverts commit ed81c2c13a94474a1e7cd6fe71cfb8bd7024c324, reversing
    changes made to 38b9622545b39f392b7c076f5a2fb9966a5a9c74.
    [system.h]
2026-02-28 Reapply "Added FSPI for LoRa RadioLib initialization and documented LoRa parameters."
    This reverts commit 3acf53c42f73119a2693d9b87b603214adb56861.
    [system.h]
2026-02-28 Fixed `DemoI2C`'s `DEMO_MODE=0` where the acknowledgment wasn't reported.
    [DemoI2C.c]
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2026-03-01 Handling errors more gracefully in `DemoSSD1306`.
    [DemoSSD1306.c]
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2026-03-03 Using watchdog timer and handling error conditions better for `MainCameraSystem`.
    [MainCameraSystem.c, Shared.py]
2026-03-03 Further improved error handling for `MainCameraSystem`.
    [MainCameraSystem.c]
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2026-03-04 Reset `MainCameraSystem`'s watchdog time-out to 10 seconds.
    [Shared.py]
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2026-03-06 Replaced `sorry`s in `_STEPPER_update_driver_once`.
    [stepper.c]
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2026-03-06 Handling `sorry` where the stepper driver can be halted into an error condition.
    [stepper.c]
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2026-03-06 Added `waking_up` and `sleeping` buzzer tunes.
    [buzzer.c]
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2026-03-07 Replaced `StepperAngularVelocities` with `StepperTuple`.
    [VehicleFlightComputer.c, stepper.c]
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2026-03-07 Handling stepper driver error conditions.
    [VehicleFlightComputer.c]
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2026-03-07 Having a `diagnostics` task to control buzzer and status LED.
    [VehicleFlightComputer.c]
2026-03-07 Reverted change to `MAX_ANGULAR_VELOCITY`.
    [VehicleFlightComputer.c]
2026-03-07 Replaced a `spinlock_us` with `FREERTOS_delay_ms`.
    [VehicleFlightComputer.c]
2026-03-07 Added `heavy_beep` buzzer tune.
    [buzzer.c]
2026-03-08 Added `chirp` buzzer tune.
    [buzzer.c]
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2026-03-08 Replaced `sorry_if` with `sus`.
    [VehicleFlightComputer.c, i2c.c, system.h]
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2026-03-08 Added `burp` and `hazard` buzzer tunes.
    [buzzer.c]
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2026-03-08 Reconfiguration of VN-100 state can be done alongside with any necessary reinitializations for hard errors.
    [VehicleFlightComputer.c]
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2026-03-09 `SPIBlock` can now also be indexed in units of 32-bit words; added additional bug assertions.
    [spi.c]
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2026-03-09 Resetting the OpenMV with `openmv_reset`.
    [VehicleFlightComputer.c]
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2026-03-10 Replaced `TV_LOGGER` with `TRANSMIT_TV`.
    [VehicleFlightComputer.c]
2026-03-11 Resetting OpenMV on time-out.
    [VehicleFlightComputer.c]
2026-03-11 Implemented counters for stepper, VN-100, OpenMV, and ESP32 issues to be logged out.
    [VehicleFlightComputer.c]
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2026-03-11 `GENERATE_DUMMY_PACKETS` no longer fills in the sequence number of the payload.
    [ESP32Vehicle.ino]
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2026-03-11 Replaced `PACKET_ESP32_START_TOKEN` and `PACKET_LORA_START_TOKEN` with strings.
    [ESP32Main.ino, ESP32Vehicle.ino, system.h]
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2026-03-12 Resetting the ESP32 on reset.
    [Shared.py, VehicleFlightComputer.c]
2026-03-12 Automatically resetting the ESP32 upon time-out.
    [ESP32Vehicle.ino, VehicleFlightComputer.c]
2026-03-12 Incrementing `esp32_issues` on each error.
    [VehicleFlightComputer.c]
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2026-03-12 Adjusted buzzer tune and delay for the `watchdog` task.
    [VehicleFlightComputer.c]
2026-03-12 Vehicle resetting when it detects it is still docked and that main is likely not powered.
    [Shared.py, VehicleFlightComputer.c]
2026-03-12 Resetting vehicle interface state after reinitialization.
    [VehicleFlightComputer.c]
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2026-03-12 Handling ESP32 timeouts with resets.
    [MainFlightComputer.c]
2026-03-13 A docked reset is done when the vehicle interface I2C bus is held down for long enough.
    [VehicleFlightComputer.c]
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2026-03-13 Bare minimum to fix `DemoGNC`.
    [GNC_MOCK_SIMULATION.csv]
2026-03-13 Fixed case-sensitivity of file path inclusion of `./deps/CMSIS-DSP/Include`.
    [Shared.py, system.h]
2026-03-13 Fixed compilation for `VehicleFlightComputer`; removed `unused` field of `OpenMVPacketGNC`.
    [OpenMV.py, VehicleFlightComputer.c]
2026-03-14 Fixed stuff up for `GNC_MOCK_SIMULATION.csv`.
    [GNC_MOCK_SIMULATION.csv]
2026-03-14 Reintroduced `PI` constant to fix compilation of `stepper.c`.
    [system.h]
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2026-03-15 Replaced `sorry` with `panic` in `DebugBoard`.
    [DebugBoard.c]
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2026-03-17 Playing buzzer tune for when a packet from the debugged-device hasn't been received in a while.
    [DebugBoard.c]
2026-03-17 Using buzzer for when any of the statuses are bad; using more LEDs for diagnostics.
    [DebugBoard.c]
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2026-03-24 Shortened narrow scan stage.
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2026-03-24 Revert "Having `SandboxNucleoBoard` mock communication with `DebugBoard`."
    This reverts commit b50777d57b0e7938c251f4c1feccffce526cbe7f.
    # Conflicts:
    # electrical/SandboxNucleoBoard.c
    [SandboxNucleoBoard.c, Shared.py]
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2026-03-24 Using LED B to indicate if the buzzer is going.
    [DebugBoard.c]
2026-03-25 Removed `live_for_too_long` reset condition.
    [VehicleFlightComputer.c]
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2026-03-30 Inducing an ESP32 reset when encountering too many consecutive CRC errors for `MainFlightComputer`.
    [MainFlightComputer.c]
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2026-04-01 Fixed the curvature check of `a`. Comparing float values to zero is nonsensical.
    [OpenMV.py]
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2026-04-01 implemented error computation
    error computation, changed evaluation of residuals from median to mean
    [OpenMV.py]
2026-04-02 Fixed changes made to `OpenMV.py`.
    [OpenMV.py]
2026-04-03 Added `missing_ok = True` to `unlink`.
    [cli.py]
2026-04-03 Fixed edge case of logging results when `ffmpeg` is not found.
    [cli.py]
2026-04-03 Using `libx265` instead of `libx264` because Windows doesn't support the latter for some reason.
    [cli.py]
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2026-04-03 Skipping checksums in `get_fields_for_csv`.
    [cli.py]
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2026-04-07 Fixed bug in I2C driver where the STOP bit was set when the hardware automatically does this for NACK conditions.
    [i2c.c]
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2026-04-09 Fixed ESP32 Arduino compilation.
    [system.h]
2026-04-13 Reintroduced buzzer into `MainFlightComputer`.
    [MainFlightComputer.c, Shared.py]
2026-04-15 Revert "Reintroduced buzzer into `MainFlightComputer`."
    This reverts commit 319fdbb5d709e46d291dfa203ae145ba011bcdd8.
    [MainFlightComputer.c, Shared.py]
2026-04-20 Fixed annotation bug; using `QQVGA` resolution.
    [OpenMV.py]
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2026-04-22 `stpy`: "Patched missing register setting for ADC configuration."
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2026-04-22 Updated `MainFlightComputerDebugStatusFlag` amongst other small fixes.
    [DebugBoard.c, MainFlightComputer.c, system.h]
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2026-04-22 Buzzer for when TE-1 is set.
    [DebugBoard.c]
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2026-04-23 finalized cvt attiude estimates
    correct error implementation
    [OpenMV.py]
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2026-04-29 Fixed typo; demonstration GIF of debug board.
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2026-04-30 Filled out the procedure for performing a battery swap.
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2026-05-01 Revert "Adjusted attitude calculation."
    This reverts commit bb1f20f053fe20ef736461b9b7ad544bd2eea8ab.
    [OpenMV.py]
2026-05-01 Removing ESP32 resets due to any sort of initialization failure.
    [ESP32Main.ino, ESP32Vehicle.ino, system.h]
2026-05-01 Replaced `CONTROLLER_ENABLE` with `CONTROLLER_MOTOR_ENABLE` where the motor control themselves can be switched.
    [VehicleFlightComputer.c]
2026-05-01 Fixed bug in `VideoMaker` when the first image frame is corrupted and the initialization `cv2.VideoWriter` is attempted anyways.
    [cli.py]
2026-05-01 Added `newline = ''` argument to avoid the issue of empty rows in the generated CSV output.
    [cli.py]
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2026-05-09 Revert "Removed the feature of sending commands to the VN-100."
    This reverts commit c71bc7cba249803ab304f12130d3dc24185fd097.
    [VehicleFlightComputer.c]
2026-05-09 Corrected the rate damping duration.
    [VehicleFlightComputer.c]
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2026-05-10 Fixed minor bug with `compressed_file_path` in `parseVideo`.
    [cli.py]
2026-05-13 Fixed division by zero.
    [VehicleFlightComputer.c]
2026-05-15 Cleaned up burn-wire assembly documentation.
